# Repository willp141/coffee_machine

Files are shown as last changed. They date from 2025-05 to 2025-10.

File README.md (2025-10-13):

☕ The Coffee Machine Project

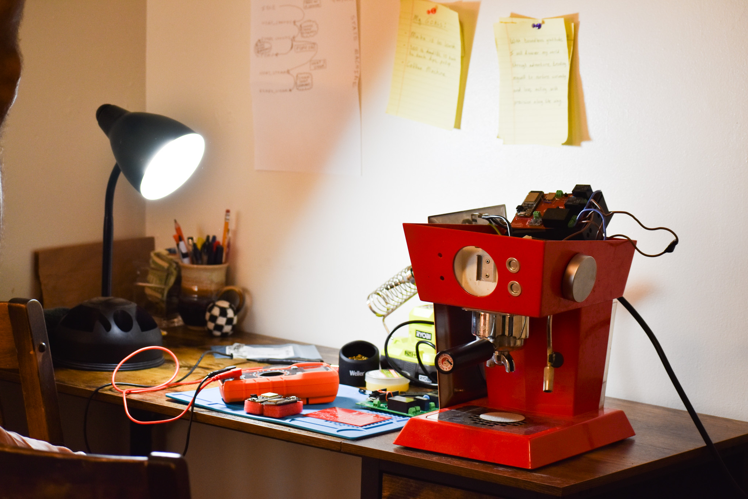
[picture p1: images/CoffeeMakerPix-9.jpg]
Coffee Machine Front


A highly over-engineered coffee machine powered by:

    ESP32 Microcontroller (Integrated radio)

    Web interface built with Micro Python

    Custom built PCB driving PUMP and BOILER relays

    MICRO SD for music storage

    Questionable life choices

Features

    Heats water (on purpose)

    Pumps water (mostly where you want it)

    Steams water (or is it just steam at that point? Steams steam?)

    Pulls a brilliant double shot (allegedly)

    Web UI so you can brew from your couch

    Pretty lights

Requirements

    Low expectations

    Coffee - has to be grind size 19, no more no less or it don't work...

    Patience

Warning

May cause excessive caffeine consumption and minor debugging-induced existential crises.

The PCB:

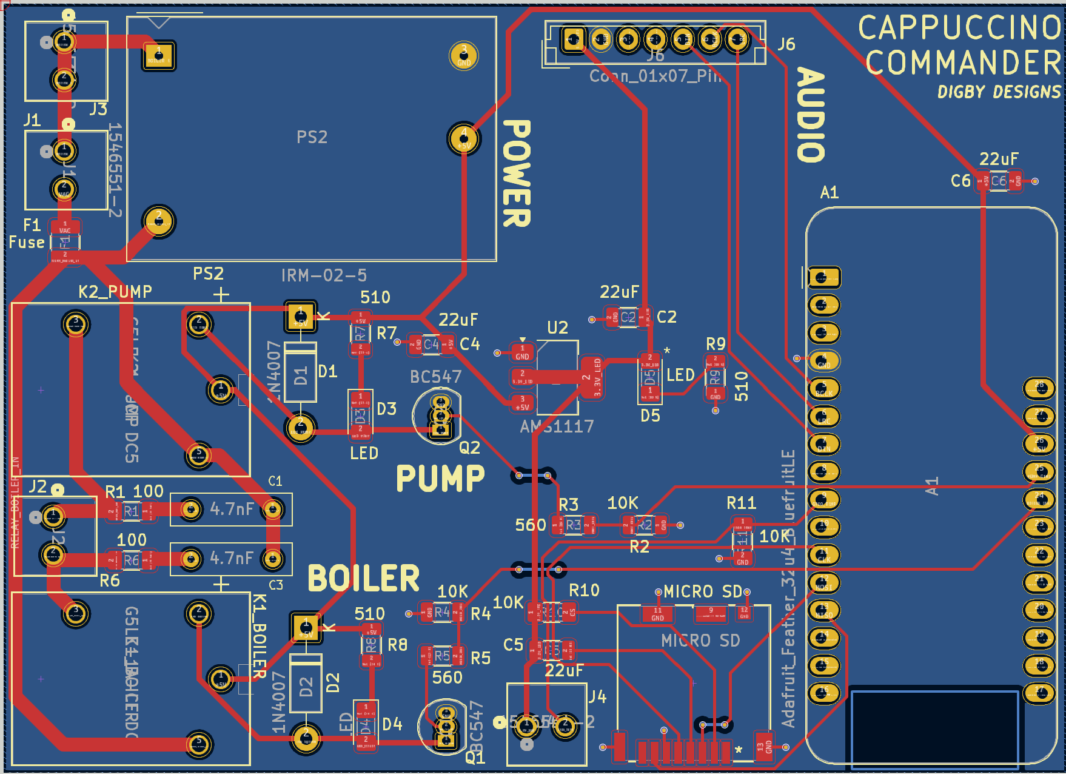
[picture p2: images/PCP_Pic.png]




The 3D Printed Housing:

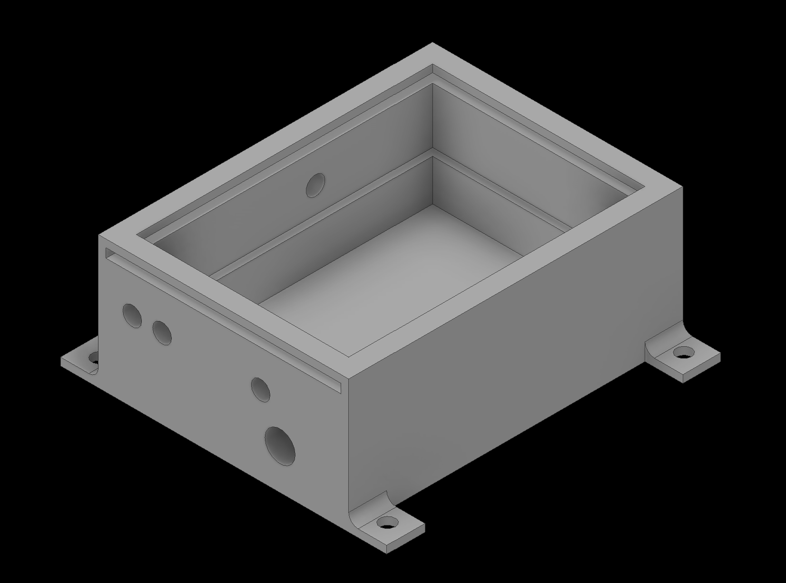
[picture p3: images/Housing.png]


Sweet, sweet success:

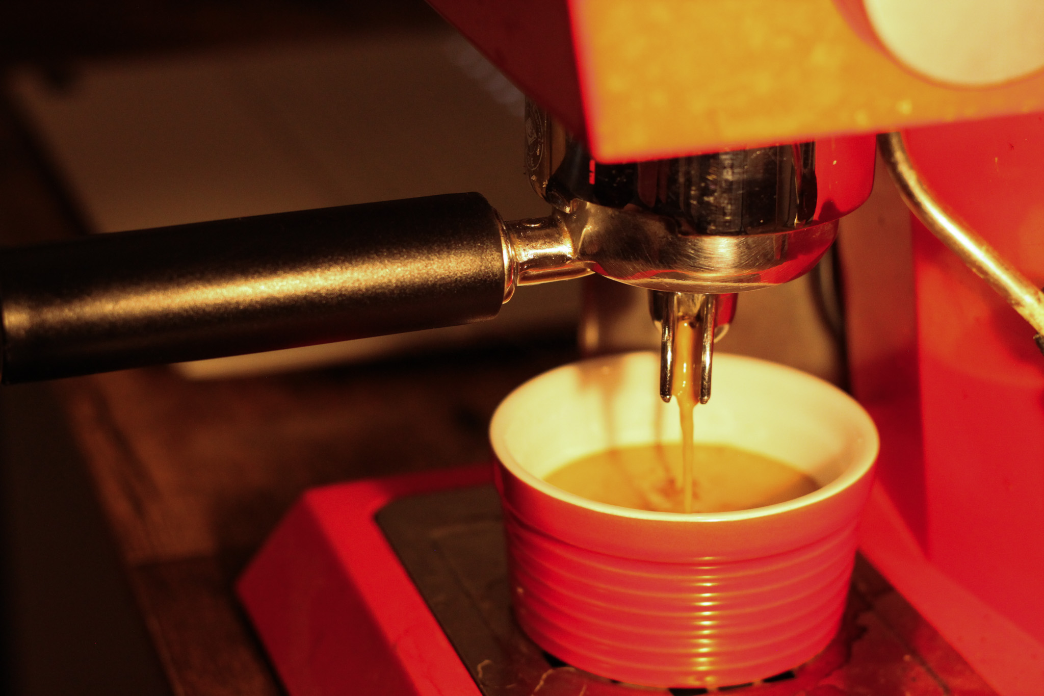
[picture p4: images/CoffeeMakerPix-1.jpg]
Coffee Machine Front


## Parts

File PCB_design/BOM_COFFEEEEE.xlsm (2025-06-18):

Reference | Value | Footprint | Qty | Cost | Aquired | Notes | Purchase Link
A1 | Adafruit_Feather_32u4_BluefruitLE | Module:Adafruit_Feather | 1 | 0 | TRUE
C1,C3 | 4.7nF | Capacitor_SMD:C_1206_3216Metric | 2 |  | TRUE | Must be special for high V/AC
C2,C4,C5 | 22uF | Capacitor_SMD:C_1206_3216Metric | 3 |  | TRUE
D1,D2 | 1N4007 | Diode_THT:D_DO-41_SOD81_P10.16mm_Horizontal | 2 |  | TRUE
D3,D4,D5 | LED | LED_SMD:LED_1206_3216Metric_Pad1.42x1.75mm_HandSolder | 3 |  | TRUE
F1 | Fuse | Fuse:Fuse_1210_3225Metric | 1 |  | TRUE
J1,J2,J3,J4 | 1546551-2 | CONN2_1546551-2_TEC | 4 |  | TRUE
J5 | DM3CS-SF | DM3CS-SF_HIR | 1 |  | TRUE
J6 | Conn_01x07_Pin | Connector_JST:JST_EH_B7B-EH-A_1x07_P2.50mm_Vertical | 1 |  | TRUE | Can I just use 7 pin connectors I have
K1PUMP1,K2BOILER1 | ALQ3F12 | ALQ3F12:RELAY_ALQ3F12 | 2 |  | TRUE
PS2 | IRM-02-5 | Converter_ACDC:Converter_ACDC_MeanWell_IRM-02-xx_THT | 1 |  | TRUE
Q1,Q2 | BC547 | Package_TO_SOT_THT:TO-92_Inline | 2 |  | TRUE | Out of Stock - replaced w/ similar
R1,R6 | 100 | Resistor_SMD:R_1206_3216Metric_Pad1.30x1.75mm_HandSolder | 2 |  | TRUE | Special for high V/AC
R2,R4,R10,R11 | 10K | -- mixed values -- | 4 |  | TRUE
R3,R5 | 560 | Resistor_SMD:R_1206_3216Metric | 2 |  | TRUE
R7,R8,R9 | 510 | Resistor_SMD:R_1206_3216Metric | 3 |  | TRUE
U2 | AMS1117 | Package_TO_SOT_SMD:SOT-223-3_TabPin2 | 1 |  | TRUE
 | Audio Board |  | 1 |  | FALSE
 | Speaker |  | 1 |  | FALSE
 | Thermistor |  | 1 |  | TRUE

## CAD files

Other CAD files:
mechanical_housing/Assembly1.iam
mechanical_housing/Board.ipt
mechanical_housing/Housing.ipt

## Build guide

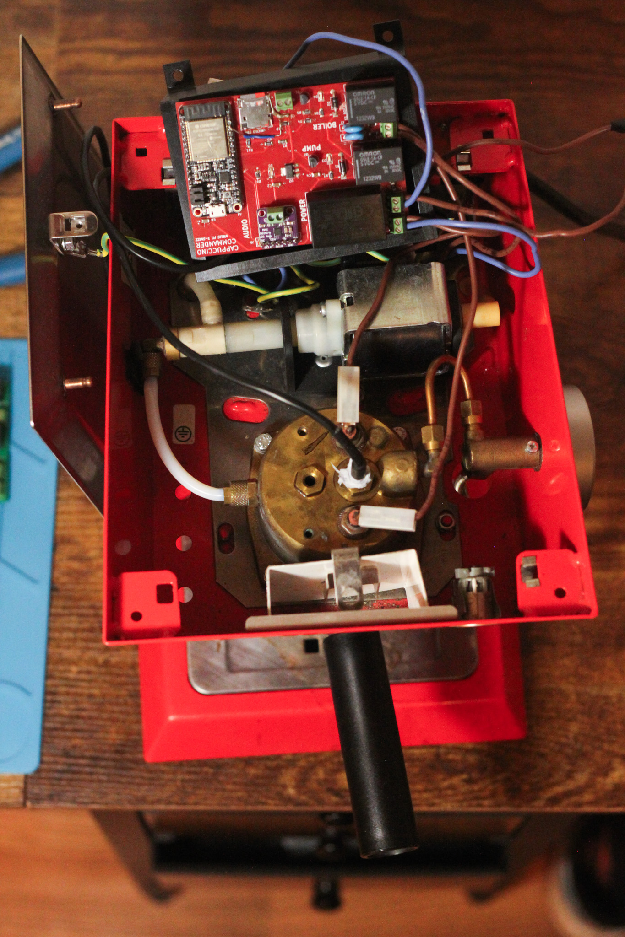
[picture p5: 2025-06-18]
images/CoffeeMakerPix-7.jpg

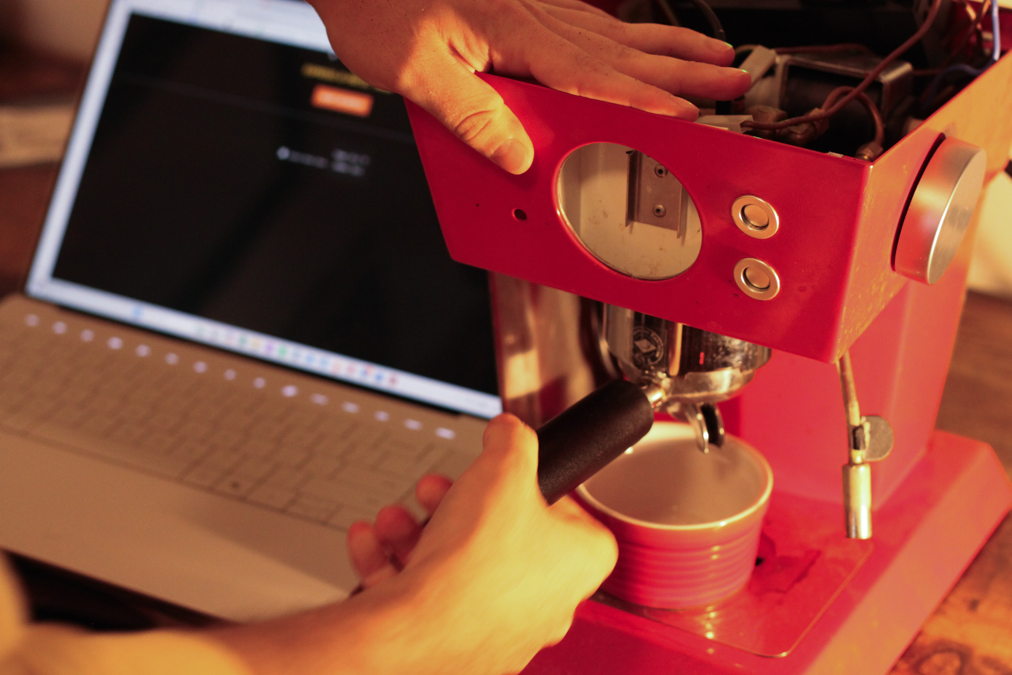
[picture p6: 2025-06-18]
images/CoffeeMakerPix-5.jpg

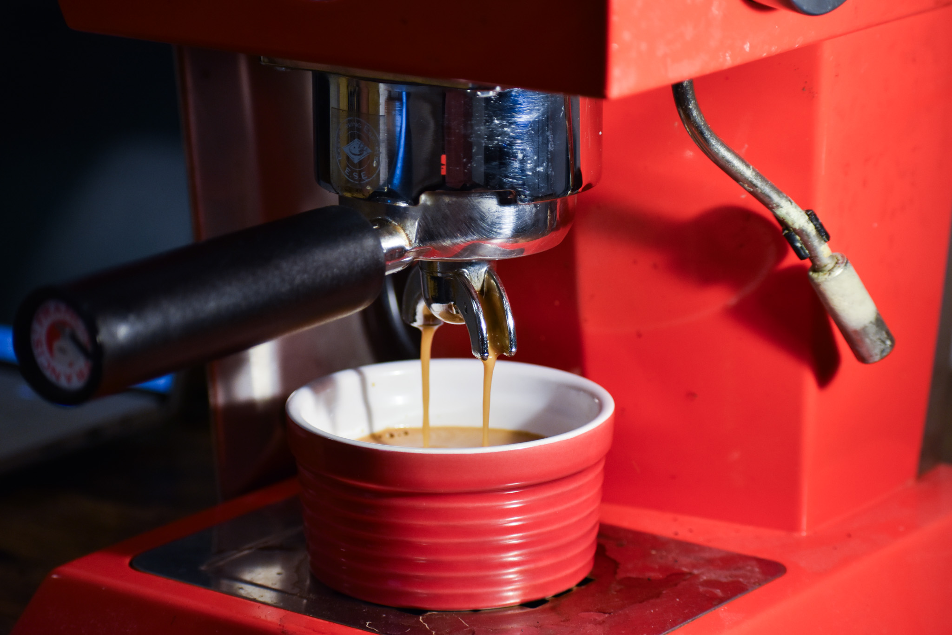
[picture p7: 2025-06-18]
images/CoffeeMakerPix-8.jpg

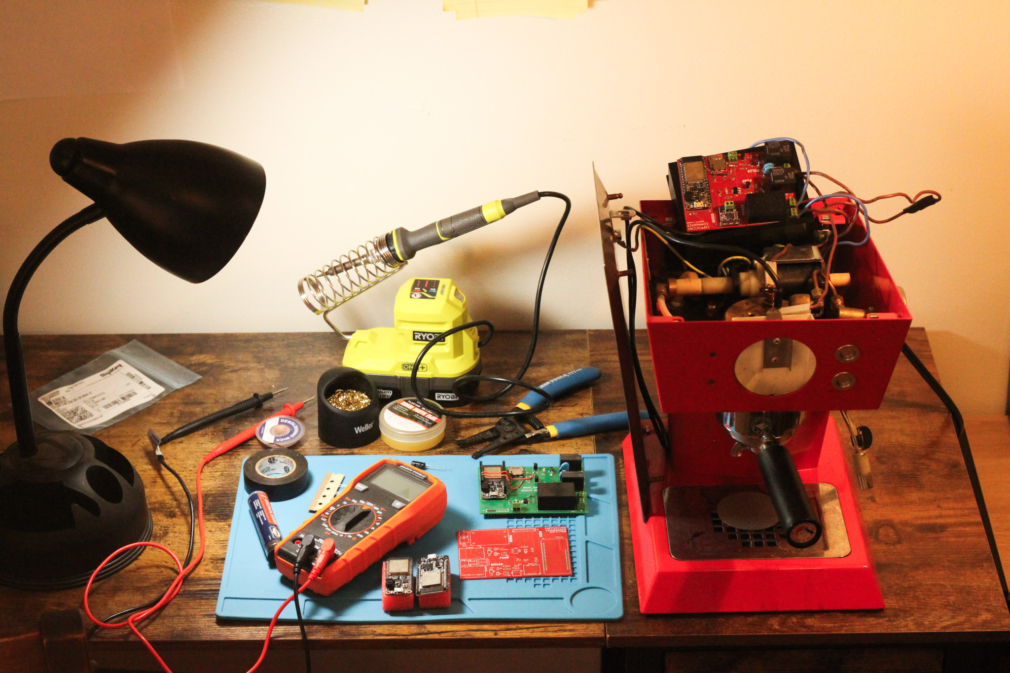
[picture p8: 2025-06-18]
images/CoffeeMakerPix-6.jpg

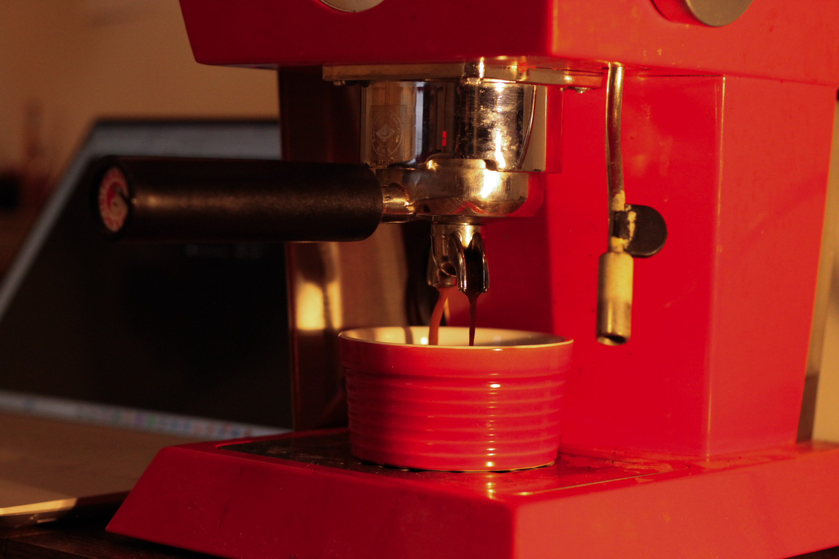
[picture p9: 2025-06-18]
images/CoffeeMakerPix-4.jpg

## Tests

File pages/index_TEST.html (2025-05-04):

# 🚀 Coffee Machine Test

🔥 HEAT UP BITCH

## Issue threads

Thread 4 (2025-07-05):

Burned/Bitter Taste

willp141, 2025-07-05:
Testing shows lower temperature results in better tasting coffee.

Reduce temp pivot to 190 degrees.

Reduce heating burst time in COFFEE_READY state to reduce temperature oscillation.

Turn OFF BOILER ON in PUMP state. Not necessary to maintain temperature with added pressure coming from coffee reducing flow.

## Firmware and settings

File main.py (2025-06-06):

################################################################################
#   Author: Will Pryor
#   Project: Coffee Machine
#   Date: 9/8/2024
#   Description: Initialize classes, start temp sensor, and run server.
################################################################################

import uasyncio as asyncio
from hardware import CoffeeMachineHardware
from stateMachine import CoffeeMachineState
from asyncServer import run_server

# Initialize hardware control and state machine
hw = CoffeeMachineHardware()
state_machine = CoffeeMachineState(hw)

# Main event loop
async def main():
	await asyncio.gather(
		asyncio.create_task(state_machine.run()),  # Start State Machine
		asyncio.create_task(hw.temp_poll_loop()),  # start Temp updater
		run_server(hw, state_machine) # Blocks forever
	)

# Start everything
if __name__ == '__main__':
	asyncio.run(main())
	

##### OLD CODE
    # from TempUpdate import tempTimer
    # import machine # type: ignore
    # import os # type: ignore
    # import sdcard # type: ignore
    # from audio import play_wav_file
    # from asyncAudio import play_wav_async
    # import time
    # import asyncio
    # from server_functions import startServer, handle_request
    # from machineManager import CoffeeMachine
    # from asyncServer import AsyncServer

    # Initialize Classes
    # coffee_machine = CoffeeMachine()

    # server = AsyncServer(
    #     coffee_machine.requestHandler, 
    #     coffee_machine.shared_data,
    #     coffee_machine.getState
    # )

    # updateTemp = tempTimer(
    #     coffee_machine.shared_data, 
    #     coffee_machine.getState, 
    #     coffee_machine.boiler.on, 
    #     coffee_machine.boiler.off,
    #     coffee_machine.check_state,
    #     coffee_machine.getTemps
    # )

    # # Audio Test Branch
    # def main():
    #     # Play the WAV file    
    #     # Ensure file exists before attempting playback
    #     play_wav()
    #     print("Played File")

    # main()

    # # asyncio Audio branch
    # async def main():
    #     await play_wav_async()

    # asyncio.run(main())
    # asyncio.run(main())

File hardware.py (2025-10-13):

import machine
import time
import uasyncio as asyncio
import ds18x20
import onewire
class CoffeeMachineHardware:
	def __init__(self):
		# GPIO setup
		self.heater_pin = machine.Pin(12, machine.Pin.OUT)
		self.pump_pin = machine.Pin(13, machine.Pin.OUT)
		self.shared_state = {
			'brew_request': False,
			'pump_request': False,
			'steam_request': False,
			'idle_request': False,
			'steam_done': False,
		}

		# DS18B20 setup
		self.onewire_pin = machine.Pin(27)
		self.temp_sensor = ds18x20.DS18X20(onewire.OneWire(self.onewire_pin))
		roms = self.temp_sensor.scan()
		if roms:
			self.sensor_rom = roms[0]  # Use first sensor found
			print("DS18B20 detected:", self.sensor_rom)
		else:
			self.sensor_rom = None
			print("No DS18B20 sensor found!")
		self.last_temp = 85  # Fallback / fake default

		# Heater Pulse control variables
		self.pulse_active = False
		self.pulse_end_time = 0
		self.pulse_armed = False

		# TEST & SIMULATION VARIABLES
		self._fake_temp = 85
		self.led = machine.Pin(2, machine.Pin.OUT)
		self.admin_override = False
		
		self.simulate_temp = False  # Turn on simulation mode for software-only testing
		self.sim_temp = 160         # Starting simulated temp
		self.sim_heating_rate = 1.0  # Degrees F per second when heater on
		self.sim_cooling_rate = 0.5  # Degrees F per second when heater off
		self.sim_last_update = time.time()

	# ---------- TEST LED ----------
	def set_led(self, state: bool):
		self.led.value(1 if state else 0)

	# ---------- HEATER CONTROL ----------
	def heater_on(self):
		if not self.admin_override:
			self.heater_pin.on()
			# TEST LED
			self.set_led(True)

	def heater_off(self):
		if not self.admin_override:
			self.heater_pin.off()
			# TEST LED
			self.set_led(False)

	# ---------- TEMP CONTROL ----------

	# Heat mode with overshoot compensation - steam and coffee modes
	async def control_temp_heat(self, target_temp):
		temp = self.last_temp
		# Thresholds
		window = 5 # 5 Degree F window for control
		# Determine if we are in steam mode or coffee mode
		if target_temp >= 250:
			# Steam mode control
			overshoot_comp = 26
			if temp >= target_temp - overshoot_comp:
				# Enter pulse mode near target
				self.heater_on()
				await asyncio.sleep(5)
				self.heater_off()
				await asyncio.sleep(5)
			else:
				# Below target - overshoot compensation: full heater ON
				self.heater_on()
		else:
			# Coffee mode control
			if self.simulate_temp == True:
				print(f"[CONTROL HEAT] Heating to {target_temp}F")
				overshoot_comp = 0
				if temp >= target_temp - overshoot_comp:
					self.heater_off()
				elif temp <= target_temp - window:
					self.heater_on()
			else:	
				overshoot_comp = 22
				if temp >= target_temp - overshoot_comp:
					self.heater_off()
				elif temp <= target_temp - window:
					self.heater_on()

	# BANG BANG Control for Coffee and Steam steady state modes
	def control_temp_ready(self, target_temp):
		temp = self.last_temp
		now = time.time()
		tight_window = 5

		if temp >= target_temp:
			self.pulse_armed = True

		print(f"[CONTROL] Temp={temp:.1f}F | Target={target_temp}F | PulseActive={self.pulse_active} | PulseArmed={self.pulse_armed}")
		# Coffee Mode
		if target_temp <= 250:
			if temp > target_temp - tight_window:
				self.pulse_armed = True
				self.heater_off()
				self.pulse_active = False

			elif temp <= target_temp - tight_window:
				if self.pulse_armed and not self.pulse_active:
					print("Starting coffee pulse")
					self.heater_on()
					self.pulse_active = True
					self.pulse_end_time = now + 7 # Pulse for X seconds - used to be 15
					self.pulse_armed = False  # Disarm until temp rises again

			if self.pulse_active and now >= self.pulse_end_time:
				self.heater_off()
				self.pulse_active = False

		# Steam Mode
		else:
			if temp >= 260:
				self.pulse_armed = True
				self.heater_off()
				self.pulse_active = False

			elif temp <= 260:
				if self.pulse_armed and not self.pulse_active:
					print("Starting steam pulse")
					self.heater_on()
					self.pulse_active = True
					self.pulse_end_time = now + 10
					self.pulse_armed = False

			if self.pulse_active and now >= self.pulse_end_time:
				self.heater_off()
				self.pulse_active = False

	# ---------- TEMP SENSOR ----------

	def get_temp(self, target=None):
		return self.last_temp

	async def temp_poll_loop(self):
		while True:
			if self.simulate_temp:
				self.update_simulated_temp()
			else:
				if self.sensor_rom:
					try:
						self.temp_sensor.convert_temp()
						await asyncio.sleep_ms(750)  # Wait for conversion
						# Read temperature in Celsius and convert to Fahrenheit
						temp_c = self.temp_sensor.read_temp(self.sensor_rom)
						if isinstance(temp_c, (float, int)):
							self.last_temp = temp_c * 9 / 5 + 32  # Convert to Fahrenheit
					except Exception as e:
						print("Temp read failed:", e)
			await asyncio.sleep(2)
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

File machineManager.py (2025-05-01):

######################################################
#   Author: Will Pryor
#   Project: Coffee Machine
#   Date: 9/8/2024
#   Description: Functionality Moved to machineManager
######################################################

from machine import Pin # type: ignore
import time
import asyncio

class State:
    DEFAULT = 0
    AUTO = 1
    GET_READY = 2
    PUMP = 3
    STEAM = 4

class CoffeeMachine:
    def __init__(self):
        print("Machine Class Initializing")
        print("     Setting State to Default")
        self.state = State.DEFAULT
        print("     Buttons and Variables Initializing")
        self.buttons = {
            'mAUTOMATIC_BUTTON': False,
            'mHEAT_WAIT_BUTTON': False,
            'mIM_READY_BUTTON': False,
            'mWANT_STEAM_BUTTON': False,
            'mDEFAULT_BUTTON': False,
            'mGO_TO_WAIT': False,
            'mCANCEL_BUTTON': False,
            'mPUMP_State': False,
            'mBOILER_State': False
        }

        # Shared data between the server and the coffee machine logic
        self.shared_data = {
            'temperature': 75,  # Example temperature
            'pump_state': False,  # Pump is initially off
            'heater_state': False,  # Heater is initially off
            'target_temp': 95, # If this updated, also need to update in default state handler
            'temp_tolerance': 5, # If this updated, also need to update in default state handler
            'mpump_on_time': 5,
            'shared_state': self.state
        }
        
        print("     Shared state is: ", self.shared_data['shared_state'])
        print("     Buttons Initialized")
        self.sse_clients = []  # Store connected SSE clients
        print("     SSE Clients Initialized")
        print("     GPIO Pins Initializing")
        self.pump = Pin(13, Pin.OUT)  # GPIO Pin for PUMP 
        self.boiler = Pin(12, Pin.OUT)  # GPIO Pin for BOILER
        
        print("     GPIO Pins Initialized")

        # # Target temperature range
        self.target_temp = 95
        self.temp_tolerance = 5

        print("Machine Class Initialized")

    def getState(self):
        current_state = self.state
        self.shared_data['shared_state'] = current_state
        # print(f"     Get State function returns {current_state}")
        return current_state
    
    def getTemps(self):
        current_temp_tolerance = self.shared_data['temp_tolerance']
        current_target_temp = self.shared_data['target_temp']
        print("     getTemps: current_temp_tolerance is now ", current_temp_tolerance)
        print("     getTemps: current_target_temp is now ", current_target_temp)
        return current_target_temp, current_temp_tolerance
    
    async def updateTemps(self, tolerance, target):
        self.shared_data['temp_tolerance'] = tolerance
        self.shared_data['target_temp'] = target
        return target, tolerance
    
    def update_button(self, button_name, button_state):
        """ Update button states and check transitions """
        if button_name in self.buttons:
            self.buttons[button_name] = button_state
            # print("Updating buttons - calling check_state")
            # self.check_state()
    
    def print_buttons(self):
        print("Buttons:")
        for button_name in self.buttons:
            print("     ", button_name, "=", self.buttons[button_name])

    async def check_state(self, Timer=None):
        """ Check current state and handle transitions """
        self.print_buttons()
        print("     check_state: Before handle shared state is: ", self.shared_data['shared_state'])
        print("     check_state: Before handle self.state is: ", self.state)
        if self.state == State.DEFAULT:
            self.handle_default_state()
        elif self.state == State.AUTO:
            self.handle_auto_state()
        elif self.state == State.GET_READY:
            self.handle_heat_wait_state()
        elif self.state == State.PUMP:
            self.handle_run_pump_state()
        elif self.state == State.STEAM:
            self.handle_steam_state()
        print("     check_state: After handle self.state is: ", self.state)
        print("     check_state: After handle shared state is: ", self.shared_data['shared_state'])
        return

    def handle_default_state(self):
        """ State 0: DEFAULT """
        self.shared_data['shared_state'] = State.DEFAULT
        # Reset defaults if returning from steam state
        if self.shared_data['target_temp'] == 120:
            self.shared_data['target_temp'] = 95
            self.shared_data['temp_tolerance'] = 5

        # Check buttons
        if self.buttons['mAUTOMATIC_BUTTON']:
            self.state = State.AUTO
            self.buttons['mAUTOMATIC_BUTTON'] = False
            self.buttons['mPUMP_State'] = False
            self.buttons['mBOILER_State'] = False
        elif self.buttons['mHEAT_WAIT_BUTTON']:
            self.state = State.GET_READY
            self.buttons['mHEAT_WAIT_BUTTON'] = False
            self.buttons['mPUMP_State'] = False
            self.buttons['mBOILER_State'] = False

        # Handle pump toggle - TEST CODE
        if self.buttons['mPUMP_State']:
            if self.shared_data['pump_state']:  # Pump is currently ON, turn it OFF
                self.pump.off()
                self.shared_data['pump_state'] = False
                self.buttons['mPUMP_State'] = False  # Reset button after toggling
                print("Pump turned OFF")
            else:  # Pump is currently OFF, turn it ON
                self.pump.on()
                self.shared_data['pump_state'] = True
                self.buttons['mPUMP_State'] = False  # Reset button after toggling
                print("Pump turned ON")
        
        # Handle boiler toggle - TEST CODE
        if self.buttons['mBOILER_State']:
            if self.shared_data['heater_state']:  # Boiler is currently ON, turn it OFF
                self.boiler.off()
                self.shared_data['heater_state'] = False
                self.buttons['mBOILER_State'] = False  # Reset button after toggling
                print("Boiler turned OFF")
            else:  # Boiler is currently OFF, turn it ON
                self.boiler.on()
                self.shared_data['heater_state'] = True
                self.buttons['mBOILER_State'] = False  # Reset button after toggling
                print("Boiler turned ON")

    def handle_auto_state(self):
        """ State 1: Heat water to coffee temp """
        self.shared_data['shared_state'] = State.AUTO
        # self.target_temp = 95
        # if self.shared_data['temperature'] >= 95:  # Hardcoded coffee temp. Replaced with line below
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

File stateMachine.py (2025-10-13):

import uasyncio as asyncio
import time

class CoffeeState:
    IDLE = 'IDLE'
    HEAT = 'HEAT'
    READY_COFFEE = 'READY_COFFEE'
    PUMP = 'PUMP'
    READY_STEAM = 'READY_STEAM'
    ERROR = 'ERROR'

class CoffeeMachineState:
    def __init__(self, hardware):
        print('Initializing State Machine')
        self.state = CoffeeState.IDLE
        self.hw = hardware  # hardware interface class
        self.mode = 'coffee'  # or 'steam'
        self.target_temp = 195  # default to coffee temp (199F)
        self.temp_window = 5  # 5 Degree F window for control

    async def run(self):
        print('Running State Machine')
        prev_state = None
        while True:
            try:
                if self.state != prev_state:
                    print(f"[STATE] → {self.state}")
                    prev_state = self.state

                if self.state == CoffeeState.IDLE:
                    await self.idle()
                elif self.state == CoffeeState.HEAT:
                    await self.heat()
                elif self.state == CoffeeState.READY_COFFEE:
                    await self.ready_coffee()
                elif self.state == CoffeeState.PUMP:
                    await self.pump()
                elif self.state == CoffeeState.READY_STEAM:
                    await self.ready_steam()
                elif self.state == CoffeeState.ERROR:
                    await self.error()
            except Exception as e:
                print(f"Exception: {e}")
                self.state = CoffeeState.ERROR
            await asyncio.sleep(0.1)

    # ---------------- STATES ----------------

    async def idle(self):
        if self.hw.admin_override:
            return
        
        self.hw.heater_off()
        self.hw.pump_off()

        if self.hw.requested_brew():
            self.mode = 'coffee'
            self.target_temp = 195  # Default coffee temp (195F)
            self.state = CoffeeState.HEAT

        elif self.hw.requested_steam():
            self.mode = 'steam'
            self.target_temp = 260  # Default steam temp (275F)
            self.state = CoffeeState.HEAT
        
        self.hw.clear_requests()

    async def heat(self):
        await self.hw.control_temp_heat(self.target_temp)
        current_temp = self.hw.last_temp  # Use latest read temp

        if self.hw.requested_idle():
            self.state = CoffeeState.IDLE
        elif current_temp >= self.target_temp - self.temp_window:
            if self.mode == 'coffee':
                self.state = CoffeeState.READY_COFFEE
            elif self.mode == 'steam':
                await asyncio.sleep(10)  # Allow time for steam temp to rise
                self.state = CoffeeState.READY_STEAM

        self.hw.clear_requests()

    async def ready_coffee(self):
        print("Calling Control Temp Ready")
        self.hw.control_temp_ready(self.target_temp)
        current_temp = self.hw.last_temp

        if self.hw.requested_idle():
            self.state = CoffeeState.IDLE
        elif self.hw.requested_steam():
            self.mode = 'steam'
            self.target_temp = 260  # Switch to steam temp
            self.state = CoffeeState.HEAT
        elif current_temp > self.target_temp + self.temp_window:
            # Stay in READY_COFFEE, don't allow pump
            pass
        elif self.hw.requested_pump():
            print("Starting pump")
            self.state = CoffeeState.PUMP

        self.hw.clear_requests()


    async def ready_steam(self):
        # timeout = 5 * 60  # 5 minutes
        # start_time = time.time()

        self.hw.control_temp_ready(self.target_temp)

        if self.hw.requested_idle():
            print("Cancel requested → IDLE")
            self.mode = 'coffee'
            self.target_temp = 199  # Reset to coffee temp
            self.state = CoffeeState.IDLE
        elif self.hw.steam_done():
            print("Steam complete → IDLE")
            self.mode = 'coffee'
            self.target_temp = 199  # Reset to coffee temp
            self.state = CoffeeState.IDLE

        self.hw.clear_requests()

    async def pump(self):
        await self.hw.run_pump(duration=25)
        self.state = CoffeeState.READY_COFFEE

    async def error(self):
        self.hw.heater_off()
        self.hw.pump_off()
        self.hw.indicate_error()
        await asyncio.sleep(1)

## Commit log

2024-09-29 Fixed update temperature code to automatically turn on/off boiler based on temp goal.
    [TempUpdate.py, asyncServer.py, machineManager.py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]
2025-06-06 Post power stabilization capacitor change.
2025-06-18 3D Printed Mechanical Housing
    [Assembly1.iam, Board.ipt, Housing.ipt]
2025-06-18 Gerber Files and BOM V2 - Cappuccino Commander
    [BOM_COFFEEEEE.xlsm]
2025-06-18 Gerber Files - V1 Bean Counter
2025-06-18 Cleaning up
    [Assembly1.iam, BOM_COFFEEEEE.xlsm, Board.ipt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]
2025-06-18 PCB and 3d Print pics
2025-06-19 Temperature Improvements
    Steam state pulse control given temp sensor temp limitation
    Improvement to coffee_ready temp control
    Cleaned current_temp calls.
2025-06-20 Fixed temp control bug
    - Added temp simulator
    - Simulator mode
    - Debugging statements
    [hardware.py, stateMachine.py]
